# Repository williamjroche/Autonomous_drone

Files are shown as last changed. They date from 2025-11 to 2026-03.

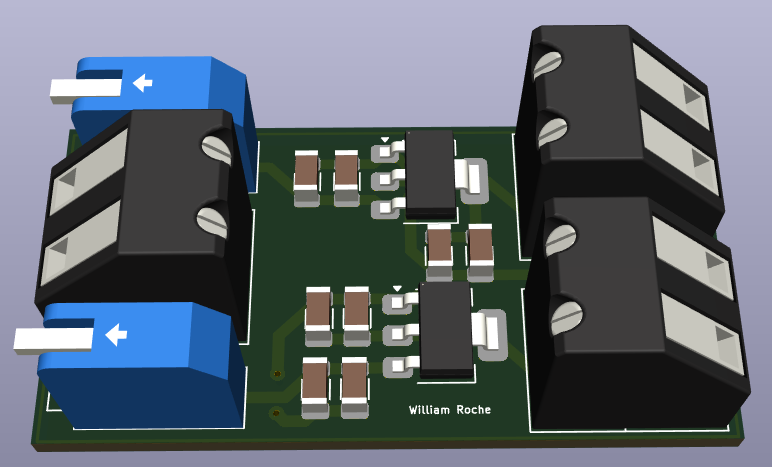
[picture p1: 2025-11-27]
dual_power_supply/dual_power_supply_pcb.png

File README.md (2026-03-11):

# Autonomous Drone

This is a GPS-Denied **Autonomous Drone** project that uses **computer vision** for flight with a **radio-transmission override**.  
The repository contains two main subsystems:

- **Flight Controller**
- **Flight Computer**

This is an **ongoing project**, and the flight controller is still in development. A prototype flight controller can be seen in the photo on the bottom. A more refined PCB implementation of this flight controller is in the works, named **'Atlas Flight Controller'**. This board uses the rp2350A microcontroller from Raspberry Pi, micro-usb power and data, ICM-20948 IMU chip (9-axis), 16MB flash memory (W25Q128JVS), an automatic power switching circuit for use with both external power and micro-usb power. This board will be powered by 5v input (from PDB) during flight which has voltage regulators for smooth and stable power delivery. 

## Flight Controller
- Software:
  - Connects to the IMU and adjusts motor speed for flight stability using PID control  
  - Implements PID control (a feedback control system that continuously adjusts an output to reach a target value)  
  - Runs the main motor-control software  
  - Includes a custom transmitter/receiver interface program
- ATLAS Flight Controller v0.6:

<p align='center'>
  
</p>

This board uses the **RP2350A** microcontroller from Raspberry Pi, micro-usb power and data, **ICM-20948 IMU** chip (9-axis), BPM 384 barometer sensor, 16MB flash memory (W25Q128JVS), an automatic power switching circuit for use with both external power and micro-usb power. This board will be powered by 5v input (from PDB) during flight which has voltage regulators for smooth and stable power delivery. This board is still in development and has not been tested yet. The current design sports a **4-layer** design, with the top and bottom for routing, second layer for GND copper pour, and the third layer for a 3.3v copper pour.

## Flight Computer

- Uses **ROS2** to send commands to the flight controller based on computer-vision input  
- Contains main computer-vision software  
- Interfaces directly with the onboard camera  

## Dual Power Supply PCB

<p align='center'>
  
</p>

- Provides regulated power for sensors and radio receiver
- Uses **PDB 12V pins** as input
- Includes both **5V and 3.3V outputs** for versatility
  - After testing the manufactured power supply, it works as expected. 12v goes into the input side, can turn each channel on or off using the blue switches.
  - 5v and 3.3v are extremely accurate and stable.
  - Minimal heat produced.
- **KiCad files included** for open access  
- **Gerber, BOM, and Pick-and-Place files** included for quick ordering

## Drone Frame

- Modified STL files sourced online and optimized for **3D printing in PLA**  
- All screw holes intended for **M3 screws** (not pre-threaded — use nuts)  
- Due to 3D-printer tolerances, some holes may require **M2 screws with nut and lock washer**  
- Ensure all screws are tightened **as much as possible** to avoid structural weakness  

## How to Use

*This repo is best used as a guide for building your own custom autonomous drone, as the implementation is specific to the materials used.*

-Materials: 3D printer, PLA filament, 4 BLDC motors (I'm using 920kv DJI), 3S lipo, 4 ESC's, 1 PDB (power distribution board), radio ELRS controller, radio ELRS to PWM receiver, Raspberry Pi 5, Raspberry Pi Pico, IMU board
- Upload all files in the **Flight Controller** folder to a **Raspberry Pi Pico** running the latest Micropython  
- Follow the GPIO mappings in `esc_control.py` and `controller_input.py`, or adjust as needed  
- Ensure BLDC motors adjacent to each other rotate in **opposite directions**
- Optional: order dual channel power distribution board for smooth and effecient power
- *Flight Computer instructions are still in progress*

My progress so far:

drone

*This is a work in progress*

MIT License

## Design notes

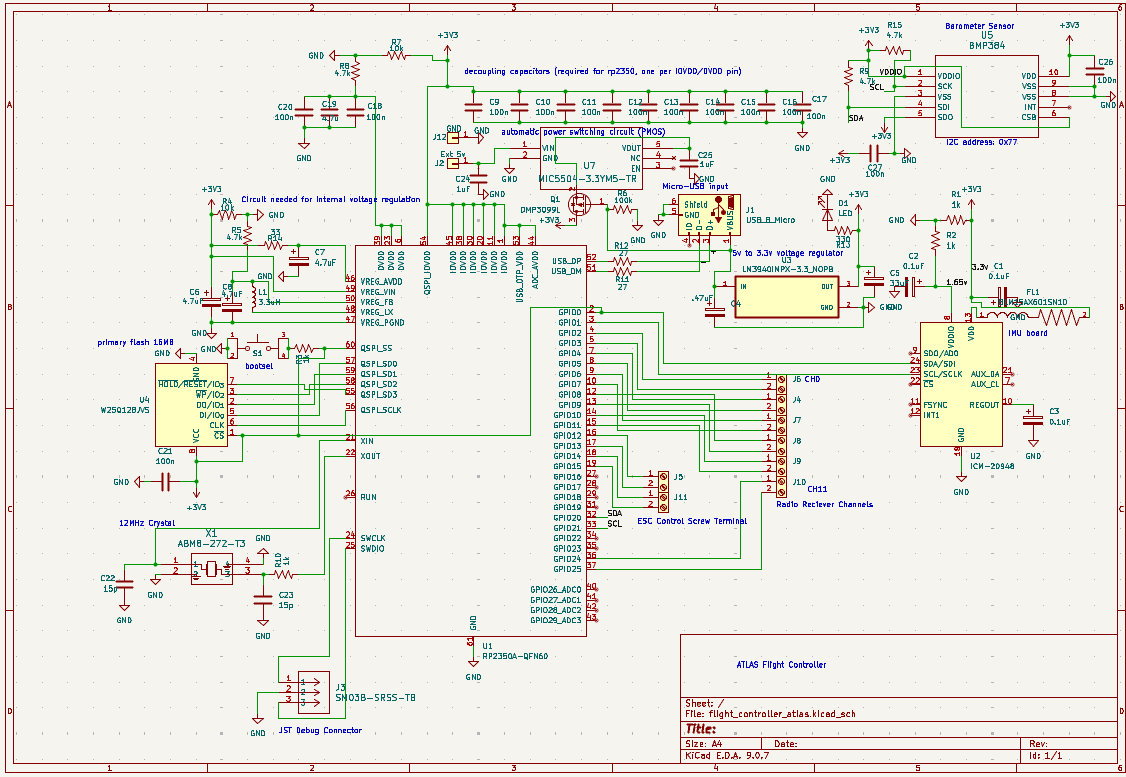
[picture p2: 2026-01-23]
flight_controller_atlas/pictures/atlas_flight_controller_schematic_v0.6.png

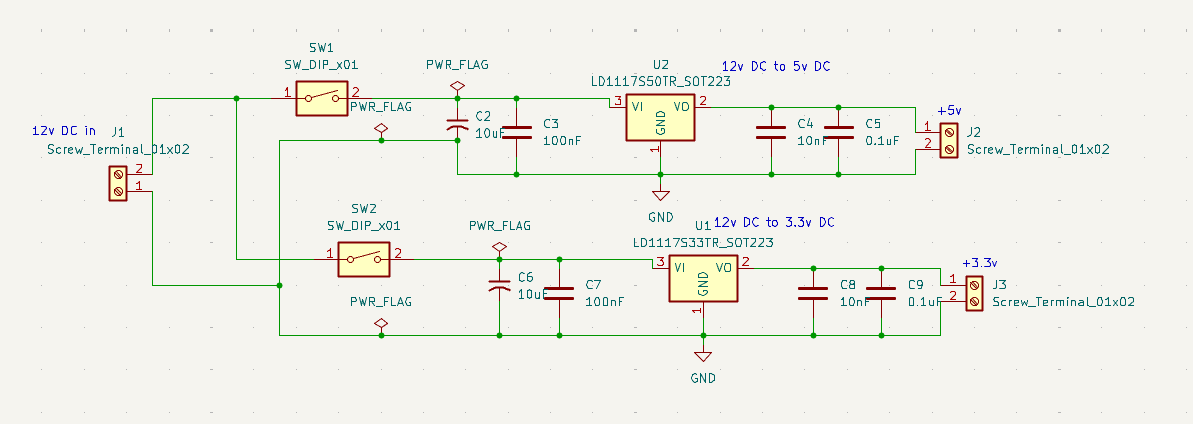
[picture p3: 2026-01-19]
dual_power_supply/dual_power_supply_schematic.png

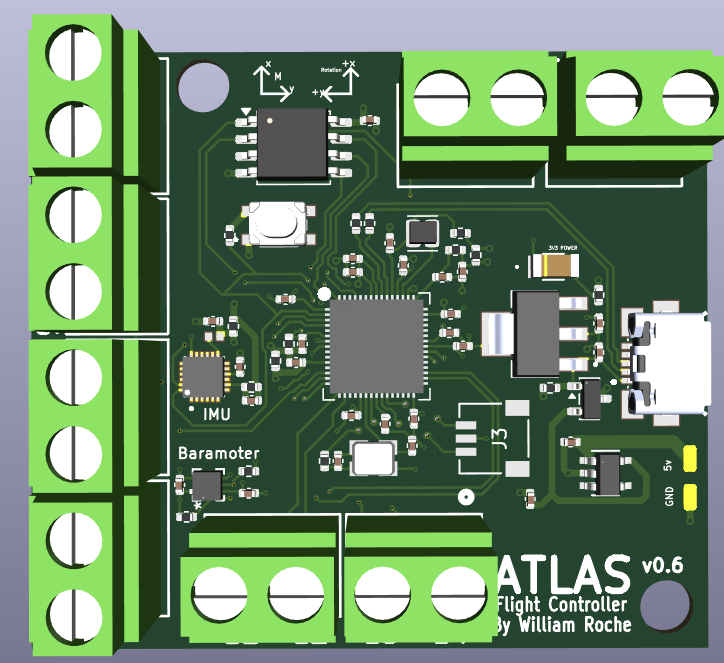
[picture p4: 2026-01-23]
flight_controller_atlas/pictures/atlas_flight_controller_pcb_3dview_v0.6.png

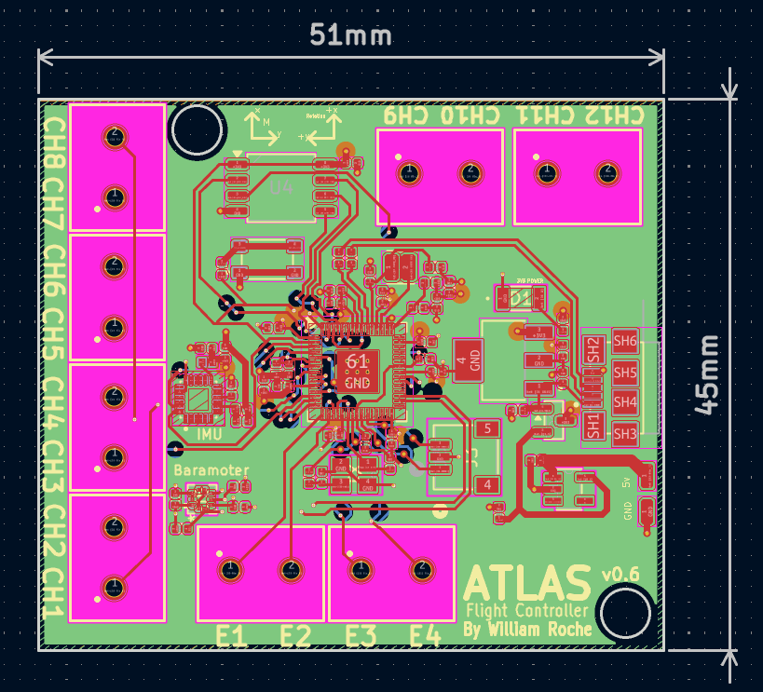
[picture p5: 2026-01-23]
flight_controller_atlas/pictures/atlas_flight_controller_pcblayout_v0.6.png

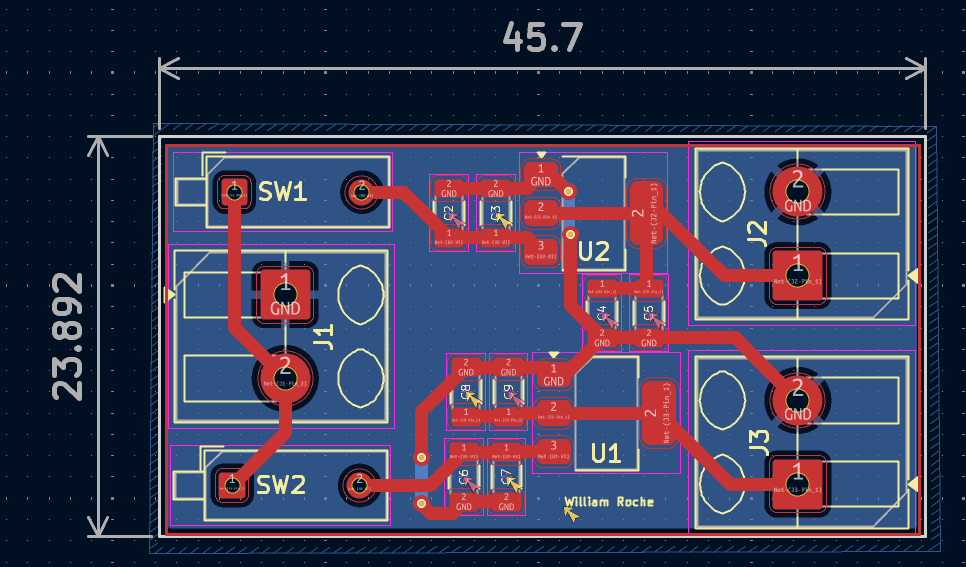
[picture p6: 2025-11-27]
dual_power_supply/dual_power_supply_pcblayout.png

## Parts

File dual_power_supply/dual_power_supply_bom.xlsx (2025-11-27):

Designator | Footprint | Quantity | Comment
C7, C3 | C_1206_3216Metric | 2 | 100nF
C5, C9 | C_1206_3216Metric | 2 | 0.1uF
C4, C8 | C_1206_3216Metric | 2 | 10nF
J3, J2, J1 | Altech_AK300_1x02_P5.00mm_45-Degree | 3 | Screw_Terminal_01x02
SW2, SW1 | SW_DIP_SPSTx01_Piano_10.8x4.1mm_W7.62mm_P2.54mm | 2 | SW_DIP_x01
C6, C2 | C_1206_3216Metric | 2 | 10uF
U1 | SOT-223-3_TabPin2 | 1 | LD1117S33TR_SOT223
U2 | SOT-223-3_TabPin2 | 1 | LD1117S50TR_SOT223

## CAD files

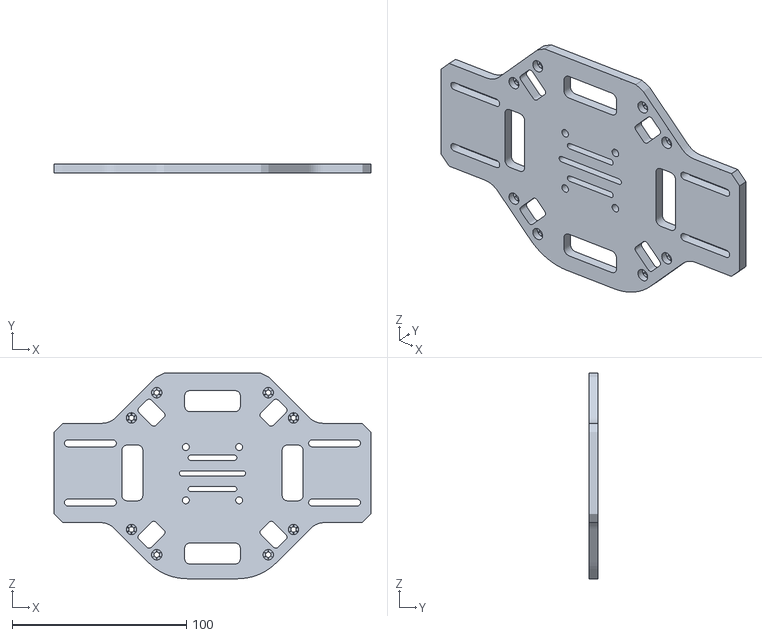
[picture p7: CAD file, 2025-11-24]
drone_frame/drone_bottom_plate.stl
182.0 x 5.00 x 118.0

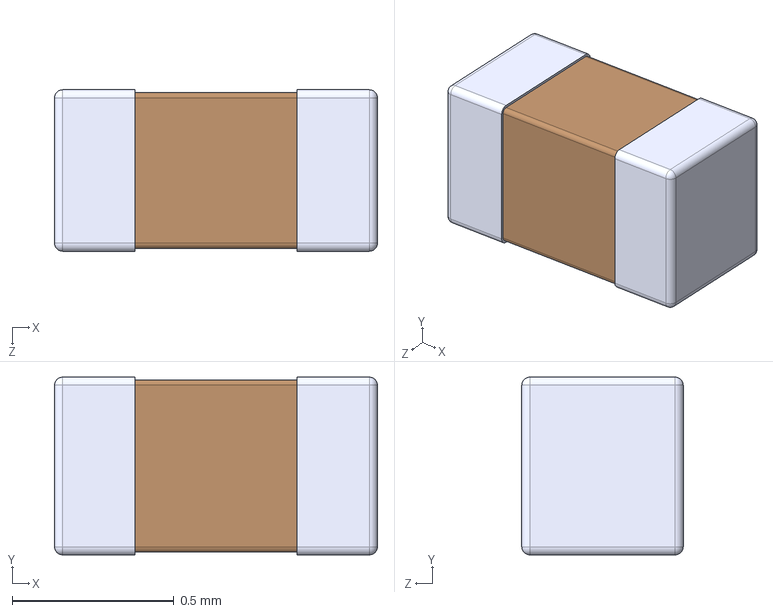
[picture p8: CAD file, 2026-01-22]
flight_controller_atlas/BLM15AX601SN1D/BLM15AX601SN1D.step
1.00 x 0.55 x 0.5 mm

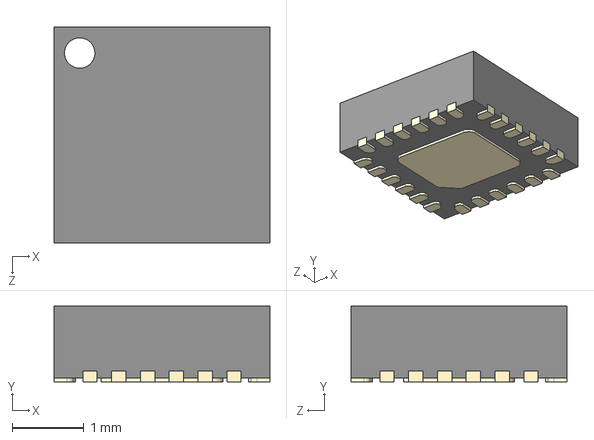
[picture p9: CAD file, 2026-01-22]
flight_controller_atlas/ICM-20948/ICM-20948.step
3.00 x 1.05 x 3.00 mm

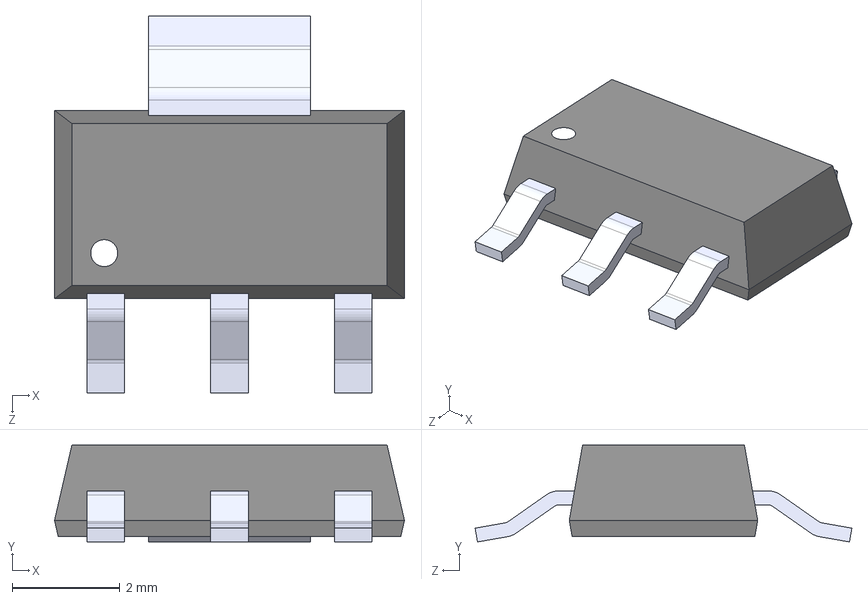
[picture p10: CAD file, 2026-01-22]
flight_controller_atlas/LD1117S33TR/LD1117S33TR.step
6.50 x 1.80 x 7.00 mm

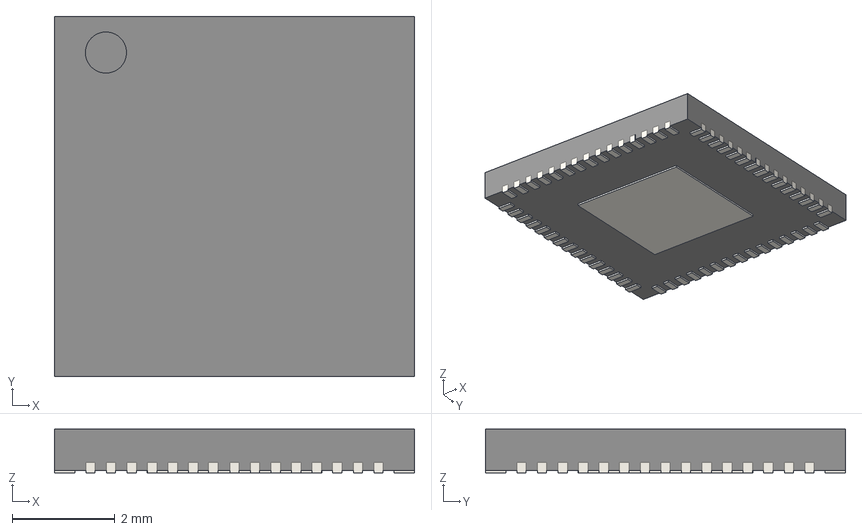
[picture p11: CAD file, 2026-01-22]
flight_controller_atlas/RP2350A-QFN60.step
7.00 x 7.00 x 0.85 mm

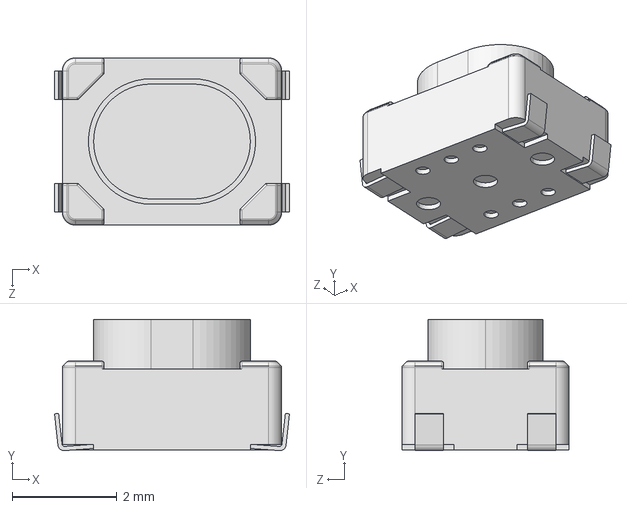
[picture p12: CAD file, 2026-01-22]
flight_controller_atlas/TL3365AF180QG/TL3365AF180QG.step
4.50 x 2.51 x 3.20 mm

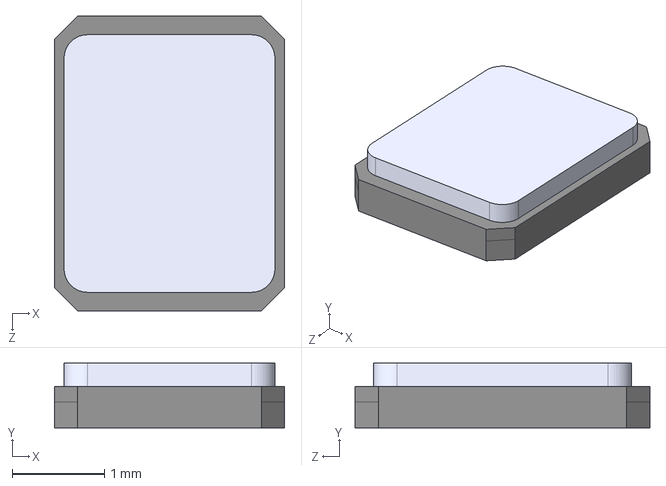
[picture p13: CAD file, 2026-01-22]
flight_controller_atlas/ul_ABM8-272-T3/ABM8-272-T3.STEP
2.50 x 0.7 x 3.20 mm

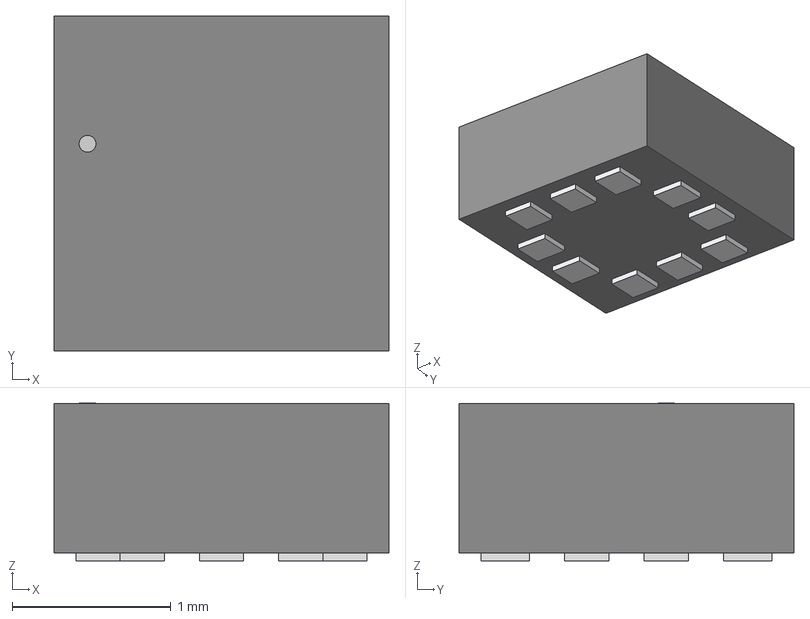
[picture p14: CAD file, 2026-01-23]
flight_controller_atlas/ul_BMP384/LGA10_2_0X2_0X0_95_BOS.step
2.11 x 2.11 x 0.993 mm

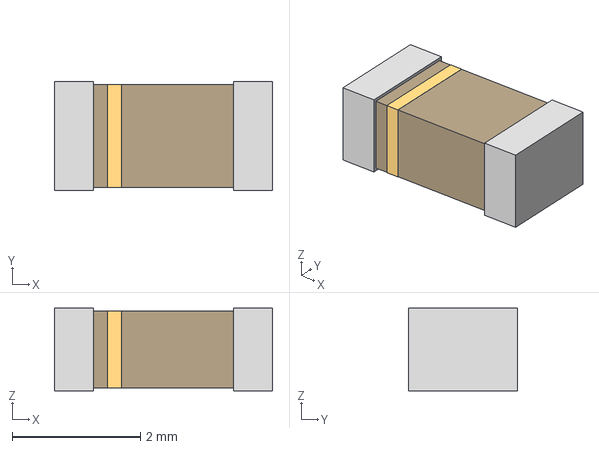
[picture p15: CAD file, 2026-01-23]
flight_controller_atlas/ul_CMD15-21VGD-TR8/LED_CMD15-21_VCC.step
3.40 x 1.70 x 1.29 mm

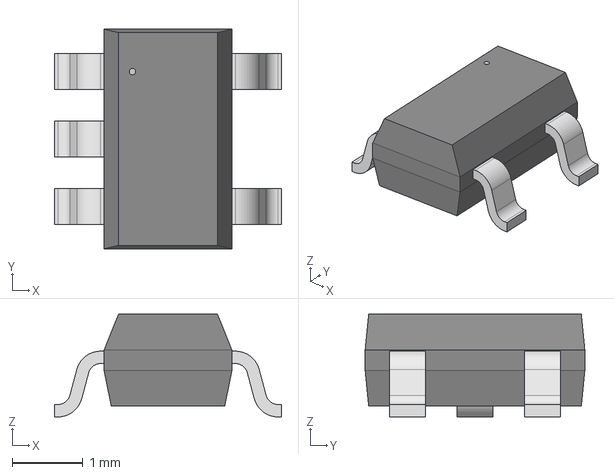
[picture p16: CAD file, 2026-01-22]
flight_controller_atlas/ul_MIC5504-3-3YM5-TR/KiCADv6/ul_MIC5504-3-3YM5-TR (1)/SOT-23-5_MC_MCH.step
3.20 x 3.10 x 1.45 mm

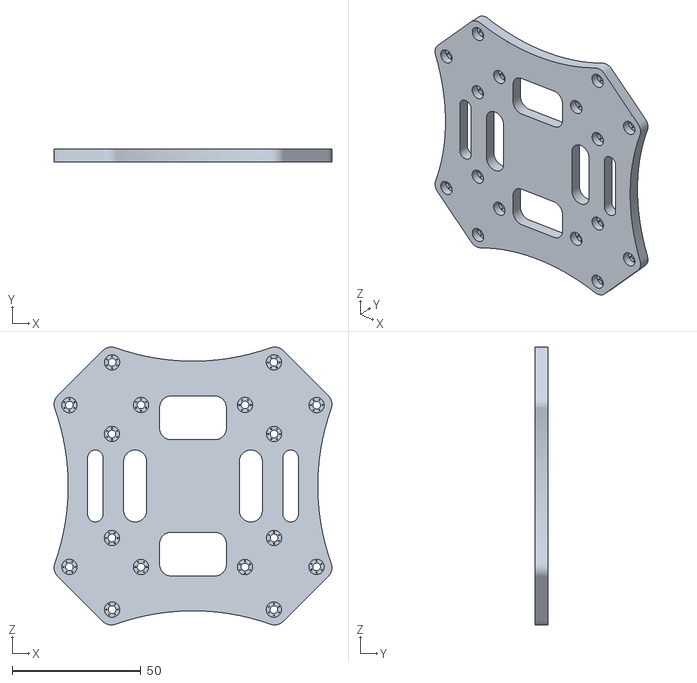
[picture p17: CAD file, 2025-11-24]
drone_frame/drone_topplate.stl
108.1 x 5.00 x 108.1

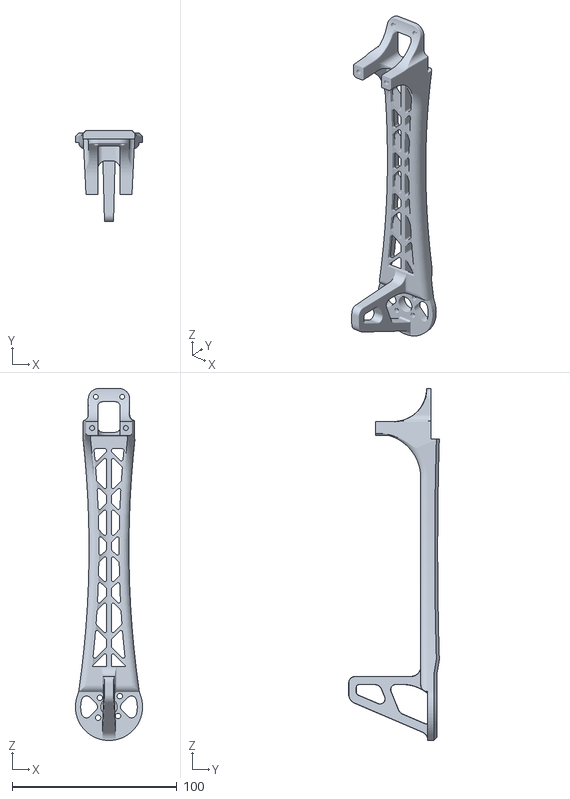
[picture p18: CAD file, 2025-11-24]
drone_frame/drone_arm.stl
40.7 x 55.0 x 213.6

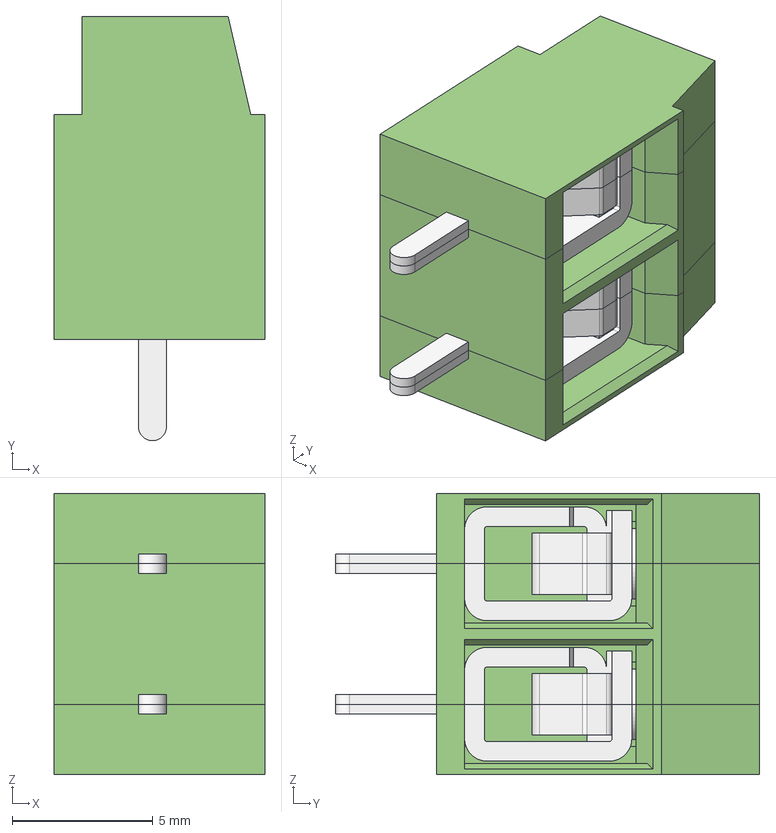
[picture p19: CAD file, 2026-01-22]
flight_controller_atlas/691137710002 (2)/691137710002.step
7.50 x 15.1 x 10.0 mm
MRT12P5_SX
MRT12P5_CNT
MRT12P5_DX

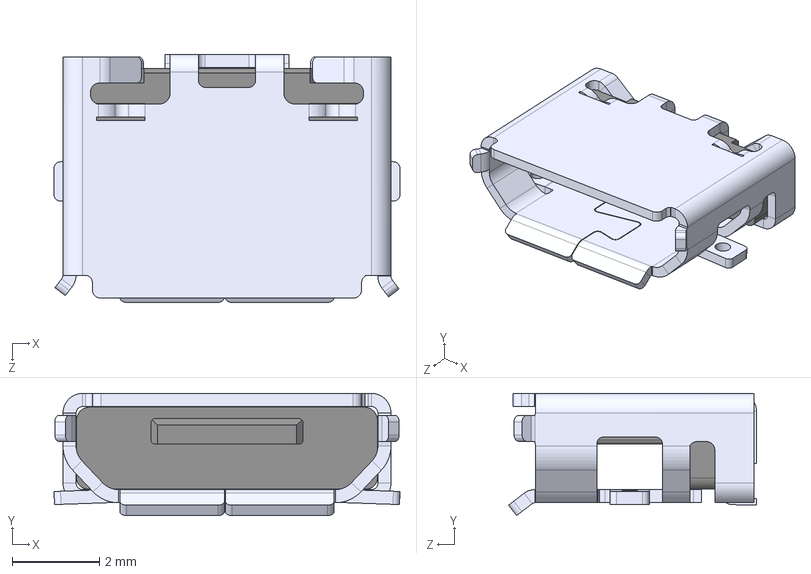
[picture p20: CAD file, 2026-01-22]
flight_controller_atlas/10118192-0001LF--3DModel-STEP-269445.STEP
7.91 x 2.79 x 5.67 mm

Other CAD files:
flight_controller_atlas/LM3940IMPX-3.3_NOPB/LM3940IMPX-3.3_NOPB.step

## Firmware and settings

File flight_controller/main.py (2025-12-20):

# MIT License
# Created by: William Roche III
# GitHub: @ williamjroche
from esc_control import ESCcontrol
from imu_icm20948 import IMU
from controller_input import DroneController
#from pid import PID
import time

#initialization and arming the ESCs/motor
esc = ESCcontrol()
#initialize IMU
imu = IMU()
#esc.esc_calibrate() #for first time use, ESCs need to be calibrated --> uncomment this line of code-->take off propellors-->run file-->delete this line of code
esc.esc_arm()

control = DroneController()

while True:
    imu.update()
    imu.test()
    throttle = control.get_throttle()
    pitch = control.get_pitch()
    roll = control.get_roll()
    yaw = control.get_yaw()
    control.print_values()
    
    #copies so we don't overwrite actual values
    roll_cmd = roll
    pitch_cmd = pitch
    
    roll_correction = roll_cmd * 0.3   #30% correction
    pitch_correction = pitch_cmd * 0.3
    
    #motor speed adjustment
    motor1_speed = throttle - pitch_correction + roll_correction
    motor2_speed = throttle - pitch_correction - roll_correction
    motor3_speed = throttle + pitch_correction - roll_correction
    motor4_speed = throttle + pitch_correction + roll_correction
    
    #convert to normalized values (-1 to 1)
    motor1_speed = max(-1, min(1, motor1_speed))
    motor2_speed = max(-1, min(1, motor2_speed))
    motor3_speed = max(-1, min(1, motor3_speed))
    motor4_speed = max(-1, min(1, motor4_speed))
    
    esc.esc_speed(motor1_speed, 1)
    esc.esc_speed(motor2_speed, 2)
    esc.esc_speed(motor3_speed, 3)
    esc.esc_speed(motor4_speed, 4)
    
    time.sleep(0.02) #updates at 50Hz

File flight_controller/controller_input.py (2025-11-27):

# MIT License
# Created by: William Roche III
# GitHub: @ williamjroche
from machine import PWM, Pin
import time
import _thread

class PWMReader:
    def __init__(self, pin_num):
        self.pin = Pin(pin_num, Pin.IN)
        self.pulse_width = 1500 #default value
        self.last_time = 0
        self.lock = _thread.allocate_lock() #used later in program so only 1 at a time access pulse width
        
        self.pin.irq(trigger=Pin.IRQ_RISING | Pin.IRQ_FALLING, handler=self._irq_handler)
        
    def _irq_handler(self, pin):
        current_time = time.ticks_us()
        
        if pin.value() == 1: #rising edge
            self.last_time = current_time
        else: #falling edge
            if self.last_time > 0:
                pulse = time.ticks_diff(current_time, self.last_time)
                
                if 800 < pulse < 2200: #set pulse defined above to pulse_width, valid PWM in range of 1000-2000 micro sec
                    with self.lock: #self.lock explained above
                        self.pulse_width = pulse
    
    def get_value(self):
        with self.lock: #self.lock explained above
            return self.pulse_width
        
    
    def get_normalized(self, min_val=-1.0, max_val=1.0): #normalizes joysticks to -1 to 1 or different min and max vals
        pulse = self.get_value()
        
        normalized = (pulse - 1500)/500.0 #we defined above that 1500 is default or 0 in our normalized vals
        
        return min_val + (normalized + 1.0) * (max_val - min_val) / 2.0 #offset + scale factor * range --> formula is used for ANY range you want
    

class DroneController:
    def __init__(self):
        self.channels = { #GPIO pins
            'throttle': PWMReader(2),
            'yaw': PWMReader(3),
            'pitch': PWMReader(4),
            'roll': PWMReader(5),
            'f1': PWMReader(6), #extra function
        }
    
    def get_channel(self, channel_name):
        if channel_name in self.channels:
           return self.channels[channel_name].get_value() #return PWM signal from channel
        return 1500 #return our define 0 if channel not found
    
    def get_all_values(self):
        return { #return all PWM signals from all channels
            'throttle': self.get_throttle(),
            'yaw': self.get_yaw(),
            'pitch': self.get_pitch(),
            'roll': self.get_roll(),
            'f1': self.get_channel('f1'),
        }
    
    def get_yaw(self):
        return self.channels['yaw'].get_normalized(-1.0, 1.0) #get yaw value between -1 and 1
    
    def get_roll(self):
        return self.channels['roll'].get_normalized(-1.0, 1.0) #get roll value between -1 and 1
    
    def get_pitch(self):
        return self.channels['pitch'].get_normalized(-1.0, 1.0) #get pitch value between -1 and 1
    
    def get_throttle(self):
        return self.channels['throttle'].get_normalized(-1.0, 1.0) #get throttle value between 0 and 1
    
    def get_f1(self):
        return self.channels['f1'].get_normalized(-1.0,1.0) #get f1 value
    
    def print_values(self): #print to terminal for debugging
        values = self.get_all_values()
        print(f"T:{values['throttle']:.2f} Y:{values['yaw']:.2f} "
              f"P:{values['pitch']:.2f} R:{values['roll']:.2f} ")

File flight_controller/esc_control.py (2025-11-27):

# MIT License
# Created by: William Roche III
# GitHub: @ williamjroche
from machine import Pin, PWM
import time

class ESCcontrol:
    def __init__(self):
        self.min_throttle = 1000000
        self.max_throttle = 2000000
        self.pwm_frequency = 50
        #ESC1 - GPIO15
        self.esc1 = PWM(Pin(15))
        self.esc1.freq(self.pwm_frequency)
        
        #ESC2 - GPIO14
        self.esc2 = PWM(Pin(14))
        self.esc2.freq(self.pwm_frequency)
        
        #ESC3 - GPIO13
        self.esc3 = PWM(Pin(13))
        self.esc3.freq(self.pwm_frequency)
        
        #ESC4 - GPIO12
        self.esc4 = PWM(Pin(12))
        self.esc4.freq(self.pwm_frequency)
        
        #list for control of all motors
        self.all_escs = [self.esc1, self.esc2, self.esc3, self.esc4]
    
    def esc_calibrate(self):
        #set all esc to min throttle
        for esc in self.all_escs:
            esc.duty_ns(self.min_throttle)
        time.sleep(2)
        #set all esc to max throttle
        for esc in self.all_escs:
            esc.duty_ns(self.max_throttle)
        time.sleep(2)
        #set all esc to min throttle
        for esc in self.all_escs:
            esc.duty_ns(self.min_throttle)
        time.sleep(2)
    
    def esc_arm(self):
        for esc in self.all_escs:
            esc.duty_ns(self.min_throttle)
        time.sleep(2)
    
    def stop_motor(self, esc):
        for esc in self.all_escs:
            esc.duty_ns(0)
    
    def esc_speed(self, normalized, motor_select):
        #map motor_select cases to the motor objects
        motor_map = {
            1: [self.esc1],
            2: [self.esc2],
            3: [self.esc3],
            4: [self.esc4],
            5: self.all_escs
        }
        duty_select = int((1500 + (500 * (normalized)))*1000)
        
        #find the motors to control based on the selection
        motors_to_control = motor_map.get(motor_select)
        #error handling
        if motors_to_control is None:
            print(f"Invalid motor: {motor_select}")
        #send speed to esc
        for esc in motors_to_control:
            esc.duty_ns(duty_select)
                
        time.sleep(0.01)

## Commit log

2025-11-11 Add files via upload
    updated MAIN, esc_control, added new IMU file
2025-11-11 Add files via upload
    changed esc_control to be a class with objects, updated imu_icm20948, changed main to reflect changes
2025-11-20 Add files via upload
    created new controller input file and updated others. The controller input file reads PWM values and normalizes them to a range of -1 to 1 (pwmreader class). The DroneController class returns values 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
2025-11-27 Add files via upload
    throttle mapping
2025-11-27 Add files via upload
    Custom power supply board for flight controller
    [bipolar_powersupply_simulation.kicad_pcb, bipolar_powersupply_simulation.kicad_sch, dual_power_supply.kicad_pcb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]
2025-11-27 Add files via upload
    updated
    [dual_power_supply.kicad_pcb, dual_power_supply.kicad_sch]
2025-11-27 Add files via upload
    Added gerber files
    [dual_power_supply-B_Cu.gbr, dual_power_supply-B_Mask.gbr, dual_power_supply-B_Paste.gbr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]
2025-11-27 Add files via upload
    files for PCB assembly. I used JLCPCB.
    [dual_power_supply_bom.xlsx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]
2025-11-27 Update README.md
    added details about gerber files
2025-12-20 Add files via upload
    Updated main to follow flight dynamics principles: added roll and pitch capability. PID control is a work in progress.
2026-01-15 Add files via upload
    Version 0.1 prototype flight controller.
    [LM3940IMPX-3.3_NOPB.step, flight_controller_atlas.kicad_pcb, flight_controller_atlas.kicad_sch]
2026-01-15 Add files via upload
    Updated Schematic, v0.2
    [flight_controller_atlas.kicad_sch]
2026-01-15 Add files via upload
    added schematic photo
2026-01-22 Add files via upload
    Atlas flight controller v0.4
    [10118192-0001LF--3DModel-STEP-269445.STEP, 691137710002.step, ABM8-272-T3.STEP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]
2026-01-23 Add files via upload
    V0.6 with barameter pt1
    [LED_CMD15-21_VCC.step, LGA10_2_0X2_0X0_95_BOS.step]
2026-01-23 Add files via upload
    v0.6 with barometer pt2
    [flight_controller_atlas.kicad_pcb, flight_controller_atlas.kicad_sch]
